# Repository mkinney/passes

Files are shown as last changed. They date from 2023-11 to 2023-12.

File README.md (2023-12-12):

# Background

Wanted the ability to mill multiple sides of something (also known as 3+1 milling). For instance, to mill the chess piece the "knight", you need to mill multiple sides. Also, wanted the ability to cut gears, but did not really want to go the really manual dividing head route. When I saw this [video by Daniel Busby](https://www.youtube.com/watch?v=1Cl9l5O7EEI) , I was inspired to make something similar.

I already had this item: [4 jaw chuck](https://a.aliexpress.com/_mOB9M1P) for when I setup a 4th axis on a PrintNC, I just needed a way to drive it. Note that in the course of working on this project, I swapped out the motor to [this one](https://www.amazon.com/gp/product/B0B6N36NQJ).

I used double sided tape to hold the items in the project box. I also had to mill out the base of the chuck as they were slightly smaller than 3/8". I plan on using T-nuts to hold the chuck down on to the table.

Here it is in operation on a manual mill (with the chuck held in a vise):


The front of the project box:
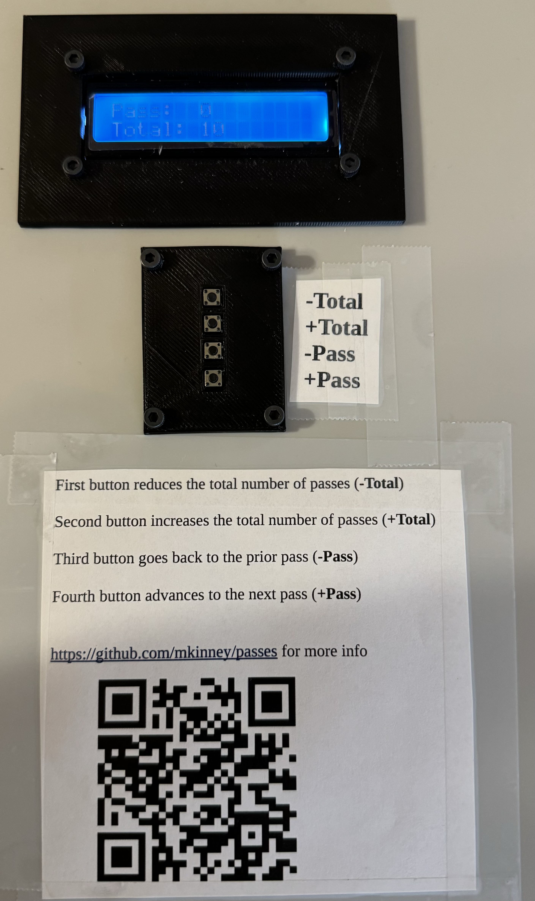
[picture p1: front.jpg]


# Components:
- [4 jaw chuck with stepper](https://a.aliexpress.com/_mOB9M1P) (went with 50:1 option)
- [stepper driver](https://www.amazon.com/gp/product/B07YWZRXGR)
- [Arduino Uno Rev3](https://www.amazon.com/dp/B008GRTSV6)
- [power supply](https://www.amazon.com/gp/product/B077BN32KZ)
- [power the arduino](https://www.amazon.com/dp/B07V6X6L89?ref=ppx_yo2ov_dt_b_product_details&th=1)
- [barrel connector](https://www.amazon.com/43x2pcs-Connectors-Security-Lighting-MILAPEAK/dp/B072BXB2Y8)
- [4 position connectors](https://www.amazon.com/gp/product/B083GR7FQF)
- [4 position keypad](https://www.amazon.com/gp/product/B07PFK5Z7L/)
- [LCD](https://www.amazon.com/dp/B07S7PJYM6)
- [box to hold everything](https://www.amazon.com/dp/B08282SQPT?ref=ppx_yo2ov_dt_b_product_details&th=1)
- [glands to keep it somewhat water resistant](https://www.amazon.com/dp/B09WQCF6TQ?ref=ppx_yo2ov_dt_b_product_details&th=1)
- [cables to make it easier to connect things](https://www.amazon.com/gp/product/B01EV70C78)

# Wiring:
- Arduino/LCD: 4 wires (5V power, ground, and two analog pins A4 and A5)
- Arduino/Keypad: 5 wires (ground, and 4 digital pins 3,4,5, and 6)
- Arduino/Stepper driver: 3 wires (ground, digital pins 8 and 9)
- Stepper motor/stepper driver: ensure each loop is together (in my case red/green is one loop, yellow/blue was the other loop); soldered on connector and cat 5 cable to make the cabling longer
- Power Supply/Stepper driver: red V+, black "ground" is V- ; there should be a green light on the stepper driver (the red light should be off); there should be a green light on the power supply
- Power Supply/Aruduino power(buck converter): red V+, black V-, DC barrel plug

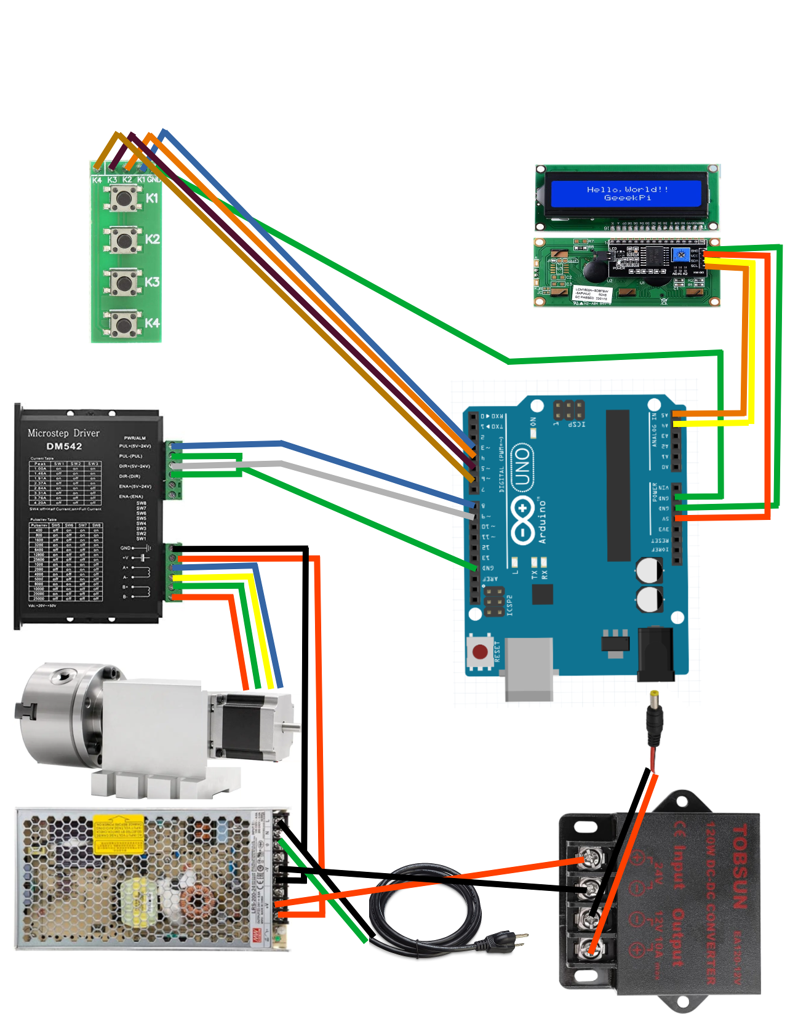
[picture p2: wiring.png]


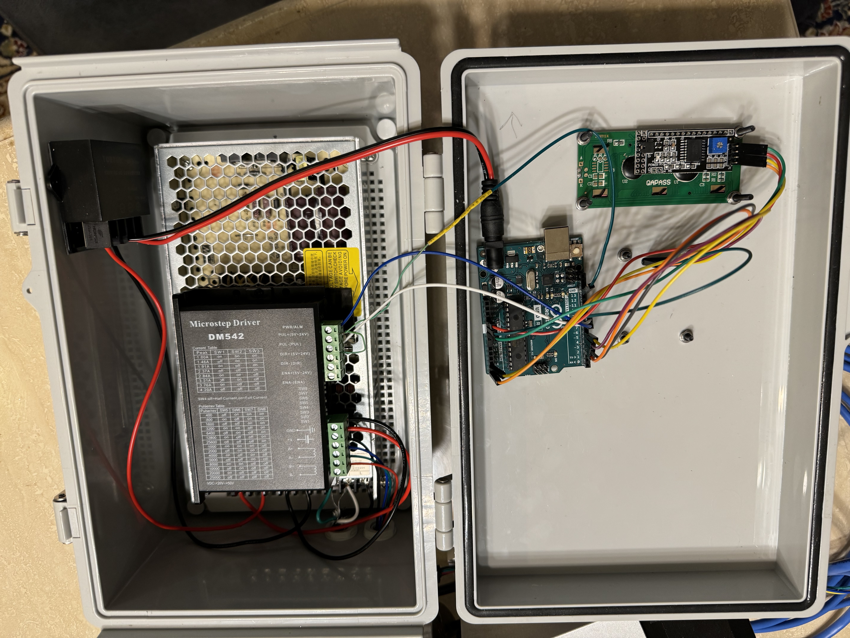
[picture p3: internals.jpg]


# Buttons:
- first button reduces the total number of passes (**-Total**)
- second button increases the total number of passes (**+Total**)
- third button goes back to the prior pass (**-Pass**)
- fourth button advances to the next pass (**+Pass**)

Typical use would be to change the number of passes you would want (example: 30 if you want 30 teeth gear). Make the first cut, then press the **+Pass** button to advance the chuck for the next cut. If you need to go back, you can press the **-Pass** button.

Initial screen:
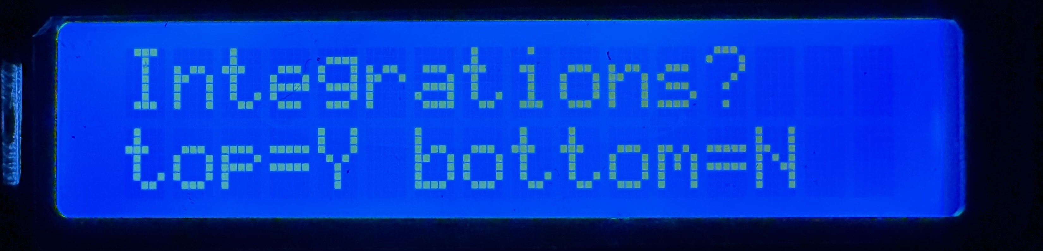
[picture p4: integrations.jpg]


Main screen:
"I=N" means the "no integration" option was selected. It would show "I=Y" if the integrations option was selected.
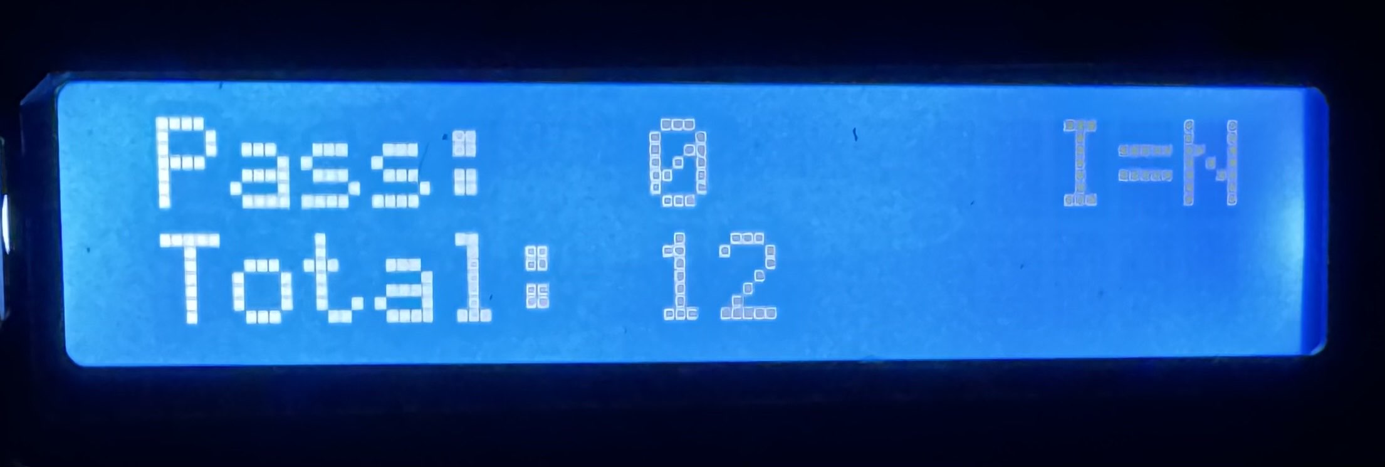
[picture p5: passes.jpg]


# Tormach integration

Integrates with Tormach mill using their [USB M-Code I/O Interface Kit](https://tormach.com/usb-m-code-io-interface-kit-32616.html)

When you power this device, be sure to press the top button to indicated that the integrations is connected. There is an indicator on the top right of the screen "I=Y" means the integrations mode is enabled. If you specify integrations, but nothing is connected on pin12, then the chuck will randomly start spinning as the Arduino "read" provides random input. [For more info](https://www.arduino.cc/reference/en/language/functions/digital-io/digitalread/)

Wiring:
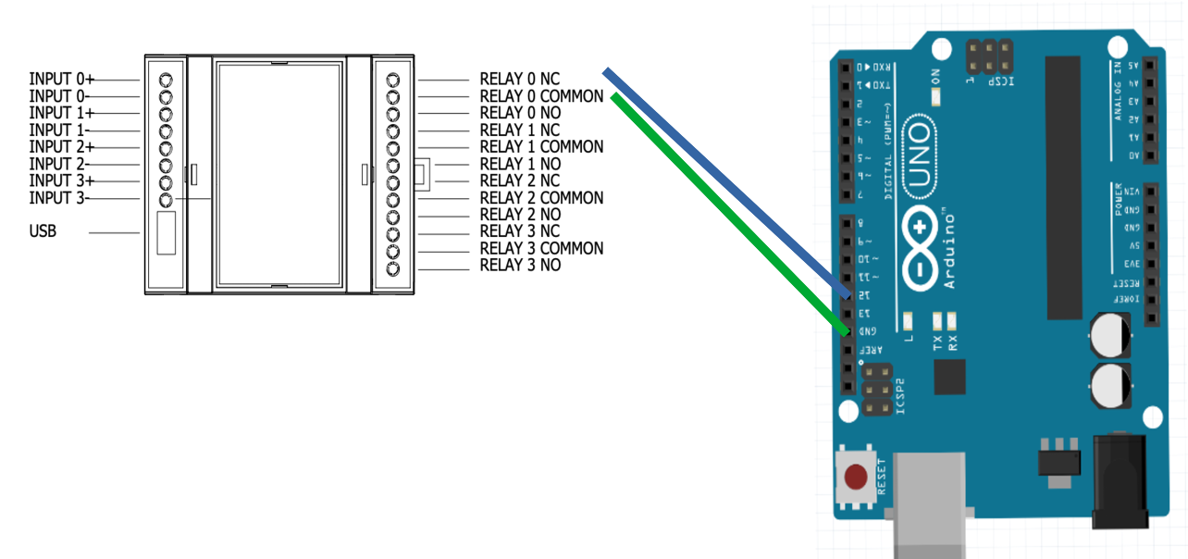
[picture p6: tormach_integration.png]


Connect the USB of the 32616 to the PathPilot computer. Go into settings and enable the "USB IO Kit". Go to the Status tab to see logging as well as new buttons:

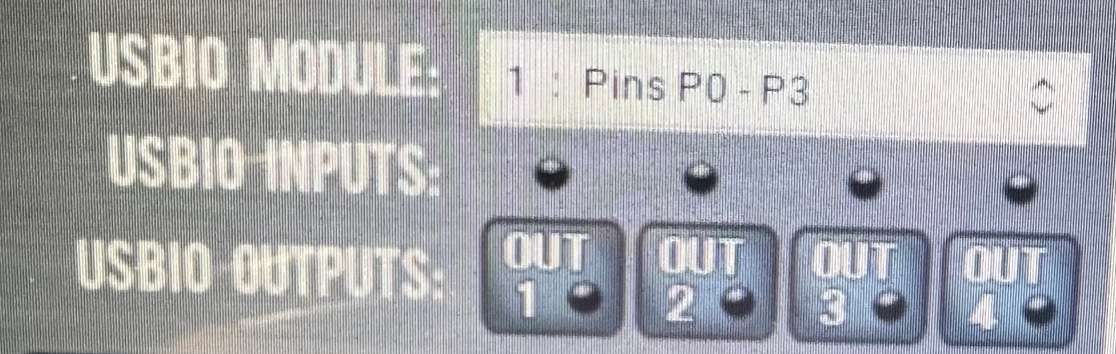
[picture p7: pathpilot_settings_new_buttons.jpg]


Send GCODE "M64 P0" to do the same as the **Pass+** button. Be sure to send the "M65 P0" on a different line, but soon after. Pressing the "OUT1" button is the same as sending the GCODE.

# Files:
- source code: [passes.ino](passes.ino)
- [lcd_faceplate.stl](lcd_faceplate.stl)
- [keypad_faceplate.stl](keypad_faceplate.stl)
- wiring diagram: [wiring.odg](wiring.odg)
- documentation for front of box: [boxdoc.odt](boxdoc.odt)

# keywords:
gear cutting, poor man's fourth axis, automated dividing head, tormach, mill, USB io, arduino, index table, dividing head, gears, 3+1

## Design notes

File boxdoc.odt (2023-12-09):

First button reduces the total number of passes (-Total)

Second button increases the total number of passes (+Total)

Third button goes back to the prior pass (-Pass)

Fourth button advances to the next pass (+Pass)

https://github.com/mkinney/passes for more info

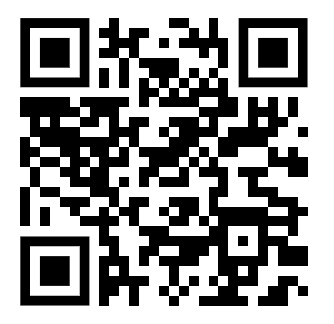
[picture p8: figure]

-Total

+Total

-Pass

+Pass

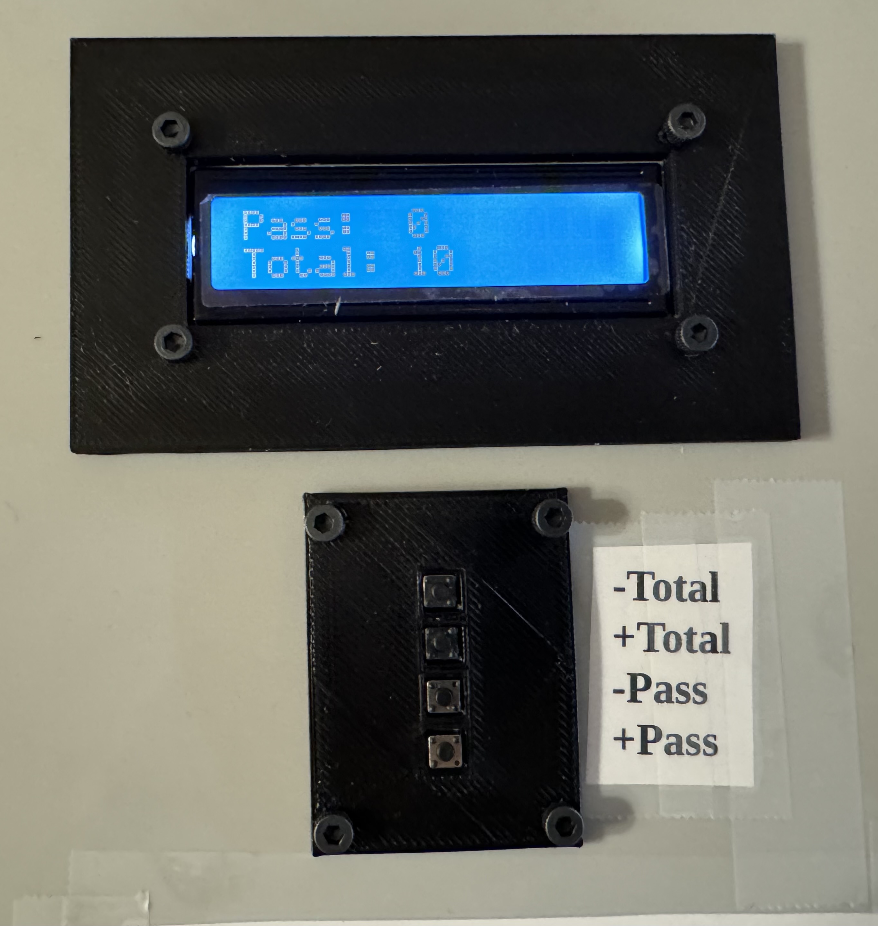
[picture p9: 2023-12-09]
front2.jpg

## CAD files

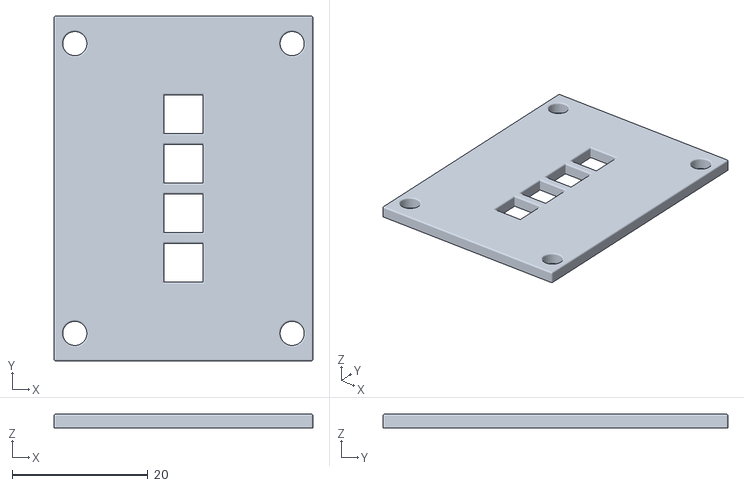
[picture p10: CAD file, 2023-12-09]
keypad_faceplate.stl
38.1 x 50.8 x 2.03

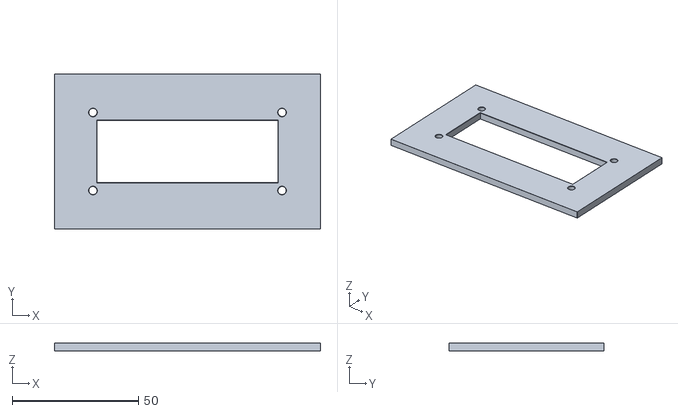
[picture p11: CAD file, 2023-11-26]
lcd_faceplate.stl
105.4 x 61.4 x 3.17

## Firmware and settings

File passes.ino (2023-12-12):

// Copyright 2023 Mike Kinney
// license is the same as the Arduino license

#include <Wire.h>
#include <LiquidCrystal_I2C.h>
#include <AccelStepper.h>

LiquidCrystal_I2C lcd(0x27, 16, 2); // set the LCD address to 0x27, if new version please use 0x3F instead.

// digital IO pins for the buttons
const int PIN_K1 = 3;
const int PIN_K2 = 4;
const int PIN_K3 = 5;
const int PIN_K4 = 6;

// digital IO pins for interaction with Tormach USB IO Part#23616
// Pin 12 on Arduino is connected to RELAY_0_NC on USB IO board
// Pin Gnd on Arduino is connected to COMMON_0 on USB IO board
const int PIN_FROM_TORMACH = 12;

// the key_delay is so we only register the button once
const int key_delay = 200;

int pass = 0;
int total = 12;

int value_read = 0;

long x = 0;

bool spinning = false;

bool integrations = false;
bool integrations_set = false;

// stepper
// digital pin8 is PUL+
// digital pin9 is DIR+
// DIR- and PUL- are connected to ground
AccelStepper stepper1(AccelStepper::DRIVER, 8, 9);

void setup() {

  lcd.init();  // initialize the lcd screen
  lcd.backlight();  // open the backlight

  Serial.begin(115200);

  // buttons
  pinMode(PIN_K1, INPUT_PULLUP);
  pinMode(PIN_K2, INPUT_PULLUP);
  pinMode(PIN_K3, INPUT_PULLUP);
  pinMode(PIN_K4, INPUT_PULLUP);

  // Tormach IO
  pinMode(PIN_FROM_TORMACH, INPUT_PULLUP);

  // Note: It cannot really go this fast
  stepper1.setMaxSpeed(400.0);
  stepper1.setAcceleration(400.0);

  //show();

  // get to "zero" position
  delay(key_delay);
  move();

  integrations = integrations_prompt();

} // setup

void clear_lcd() {
  String blanks = "                    ";
  lcd.setCursor(0, 0);
  lcd.print(blanks);
  lcd.setCursor(0, 1);
  lcd.print(blanks);
}

bool integrations_prompt() {
  lcd.setCursor(0, 0);
  lcd.print("Integrations?    "); // be sure to clear the last few characters
  lcd.setCursor(0, 1);
  lcd.print("top=Y bottom=N");
}

void show() {
  clear_lcd();
  lcd.setCursor(0, 0);
  lcd.print("Pass:");  // 1st line on lcd display

  lcd.setCursor(7, 0);
  lcd.print(pass);

  // indicator for integrations
  lcd.setCursor(13, 0);
  if (integrations) {
    lcd.print("I=Y"); // yes, integrations is enabled
  } else {
    lcd.print("I=N"); // no
  }

  lcd.setCursor(0, 1); // 2nd line on lcd display
  lcd.print("Total:");

  lcd.setCursor(7, 1);
  lcd.print(total);
} // show

void move() {
  // stepper dips
  // 1=ON 2=ON 3=OFF 4=ON
  // the motor can take 3.0A, so configured for 2.8A and full current
  // 5=OFF 6=ON 7=ON 8=ON 400 pulses/rev
  // not sure why the magical number below works (derived from trial and error)
  x = (float)pass / (float)total * 360.0 * 55.55;
  delay(1000);
  spinning = true;
	stepper1.moveTo(x);
} // move 

void loop() {
  
  if (!digitalRead(PIN_K1)) {
    if (!integrations_set) {
      integrations = true;
      integrations_set = true;
      total++;
    }
    total--;
    pass = 0;
    show();
    delay(key_delay);
  }

  if (!digitalRead(PIN_K2)) {
    total++;
    pass = 0;
    show();
    delay(key_delay);
  }

  if (!digitalRead(PIN_K3)) {
    pass--;
    show();
    delay(key_delay);
    move();
  }

  if (!digitalRead(PIN_K4)) {
    if (!integrations_set) {
      integrations = false;
      integrations_set = true;
      pass--;
    }
    pass++;
    show();
    delay(key_delay);
    move();
  }

  if (integrations) {
    // from docs: https://www.arduino.cc/reference/en/language/functions/digital-io/digitalread/
    // "If the pin isn’t connected to anything, digitalRead() can return either HIGH or LOW (and this can change randomly)."
    value_read = digitalRead(PIN_FROM_TORMACH);
    if ((!spinning) && (value_read == HIGH)) {
        pass++;
        show();
        move();
    }
    if (stepper1.run()) {
      // .run() returns true if it is still turning
    } else {
      // once the stepper is done turning, turn off our boolean
      if (spinning) {
        spinning = false;
      }
    }
  } else { // no integration
    stepper1.run();
  }

} // loop

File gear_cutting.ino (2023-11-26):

#include <Wire.h>
#include <LiquidCrystal_I2C.h>
#include <AccelStepper.h>

LiquidCrystal_I2C lcd(0x27, 16, 2); // set the LCD address to 0x27, if new version please use 0x3F instead.

// digital IO pins for the buttons
const int PIN_K1 = 3;
const int PIN_K2 = 4;
const int PIN_K3 = 5;
const int PIN_K4 = 6;

// the key_delay is so we only register the button once
const int key_delay = 200;

int tooth_num = 0;
int total_teeth = 10;

long x = 0;

// stepper
// digital pin8 is PUL+
// digital pin9 is DIR+
// DIR- and PUL- are connected to ground
AccelStepper stepper1(AccelStepper::DRIVER, 8, 9);

void setup() {

  lcd.init();  // initialize the lcd screen
  lcd.backlight();  // open the backlight

  // buttons
  Serial.begin(115200);
  pinMode(PIN_K1, INPUT_PULLUP);
  pinMode(PIN_K2, INPUT_PULLUP);
  pinMode(PIN_K3, INPUT_PULLUP);
  pinMode(PIN_K4, INPUT_PULLUP);

  stepper1.setMaxSpeed(400.0);
  stepper1.setAcceleration(400.0);
  
  delay(1000);
  stepper1.moveTo(0);
  delay(1000);

  show();

} // setup

void show() {
  lcd.setCursor(0, 0);
  lcd.print("Tooth num:");  // 1st line on lcd display

  // "clear" prior number
  lcd.setCursor(12, 0);
  lcd.print("   ");

  lcd.setCursor(12, 0);
  lcd.print(tooth_num);

  lcd.setCursor(0, 1); // 2nd line on lcd display
  lcd.print("Total teeth:");

  // "clear" prior number
  lcd.setCursor(13, 1);
  lcd.print("   ");

  lcd.setCursor(13, 1);
  lcd.print(total_teeth);
} // show

void move() {
  x = (float)tooth_num / (float)total_teeth * 360.0 * 50.0;    
  delay(1000);
	stepper1.moveTo(x);
} // move 

void loop() {
  
  if (!digitalRead(PIN_K1)) {
    total_teeth--;
    show();
    delay(key_delay);
  }

  if (!digitalRead(PIN_K2)) {
    total_teeth++;
    show();
    delay(key_delay);
  }

  if (!digitalRead(PIN_K3)) {
    tooth_num--;
    show();
    delay(key_delay);
    move();
  }

  if (!digitalRead(PIN_K4)) {
    tooth_num++;
    if (tooth_num >= total_teeth) {
      tooth_num = 0;
    }
    show();
    delay(key_delay);
    move();
  }

  stepper1.run();

} // loop

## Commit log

2023-11-12 got buttons/lcd mostly working as desired
2023-11-25 working; but stepper is getting hot
2023-11-26 add wiring and readme
2023-11-26 add info about buttons
2023-11-26 add faceplates
    [keypad faceplate v1.stl, lcd faceplate v1.stl]
2023-11-26 change the arduino power setup
2023-11-26 changes to keypad faceplate
    [keypad faceplate v1.stl, keypad faceplate.stl]
2023-11-26 remove version from the lcd stl file
    [lcd faceplate.stl]
2023-11-26 minor tweaks to the keypad holes in the stl file
    [keypad faceplate.stl]
2023-12-08 fixed doc in code, ensured dips are at 400 revs
    [passes.ino]
2023-12-09 updated readme for motor change
2023-12-09 updated keypad stl
    [keypad faceplate.stl]
2023-12-09 change filenames to not have spaces
    [keypad_faceplate.stl, lcd_faceplate.stl]
2023-12-12 temp remove the Tormach USB integration to test on a manual mill
2023-12-12 change working video with one that is actually cutting gears
